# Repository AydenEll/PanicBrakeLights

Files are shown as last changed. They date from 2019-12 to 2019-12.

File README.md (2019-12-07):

# PanicBrakeLights [Version 1.0]
This repository shows how to add an automatically activated supplementary brake light system to a motorcycle.  The system will activate and strobe to attract attention when greater than average braking force is sensed.

Repository Contents
=========================
* **/img** - Image files for the README file
* **/hardware** - Circuit design information
* **/src** - Project code (*.ino file for Arduino)
* **/LICENSE** - The user license file (open)
* **/README.md** - Project guide (this document)

Requirements and Materials
=========================

**Libraries required:**
* **Adafruit ADXL343 by Adafruit** - [Adafruit ADXL343 Accelerometer Driver](https://github.com/adafruit/Adafruit_ADXL343)
* **Adafruit Unified Sensor by Adafruit** - [Adafruit Unified Sensor Driver](https://github.com/adafruit/Adafruit_Sensor)
* **Adafruit NeoPixel by Adafruit** - [Adafruit NeoPixel Library](https://github.com/adafruit/Adafruit_NeoPixel)

**Materials required:**
* Arduino-based microcontroller: [Adafruit Metro Mini](https://www.adafruit.com/product/2590) is used in my implementation (Adafruit Product ID 2590)
* [Adafruit ADXL343 Triple-Axis Accelerometer](https://www.adafruit.com/product/4097) (Adafruit Product ID 4097)
* Weather-resistant adhesive-backed LED strips: strips of WS2812B individually addressable LED modules such as [Adafruit NeoPixels](https://www.adafruit.com/product/1138) will be used--they are individually addressable and can be cut to any length (as small as one LED element)
* LM2596 DC-to-DC buck converter to step 12V down to 5V (to power system off motorcycle battery)
* Small breadboard to act as substrate and to maintain proper alignment of accelerometer
* Assorted bulk wire, jumper wires, and shrink tube
* Soldering station and soldering supplies including solder, flux, desoldering tools/wick, and a "third hand"

Build Instructions
=========================
The main circuit assembly is quite straightforward.  Using a small breadboard as a substrate, connect your Metro Mini, ADXL343, and LED strips (left and right) with the step-down power converter according to the following breadboard diagram and wiring schematic:
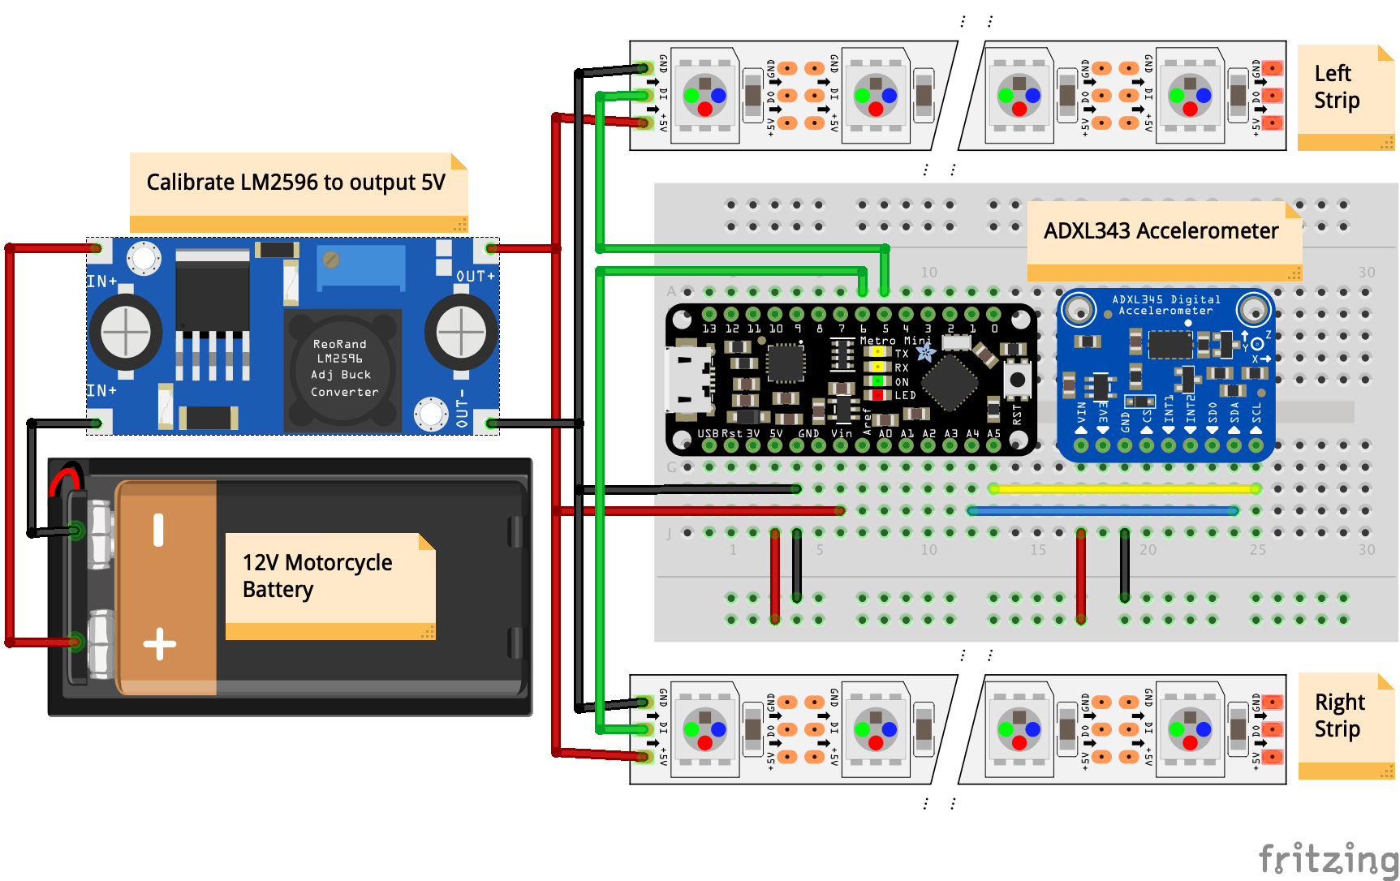
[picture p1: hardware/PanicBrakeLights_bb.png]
Breadboard Diagram

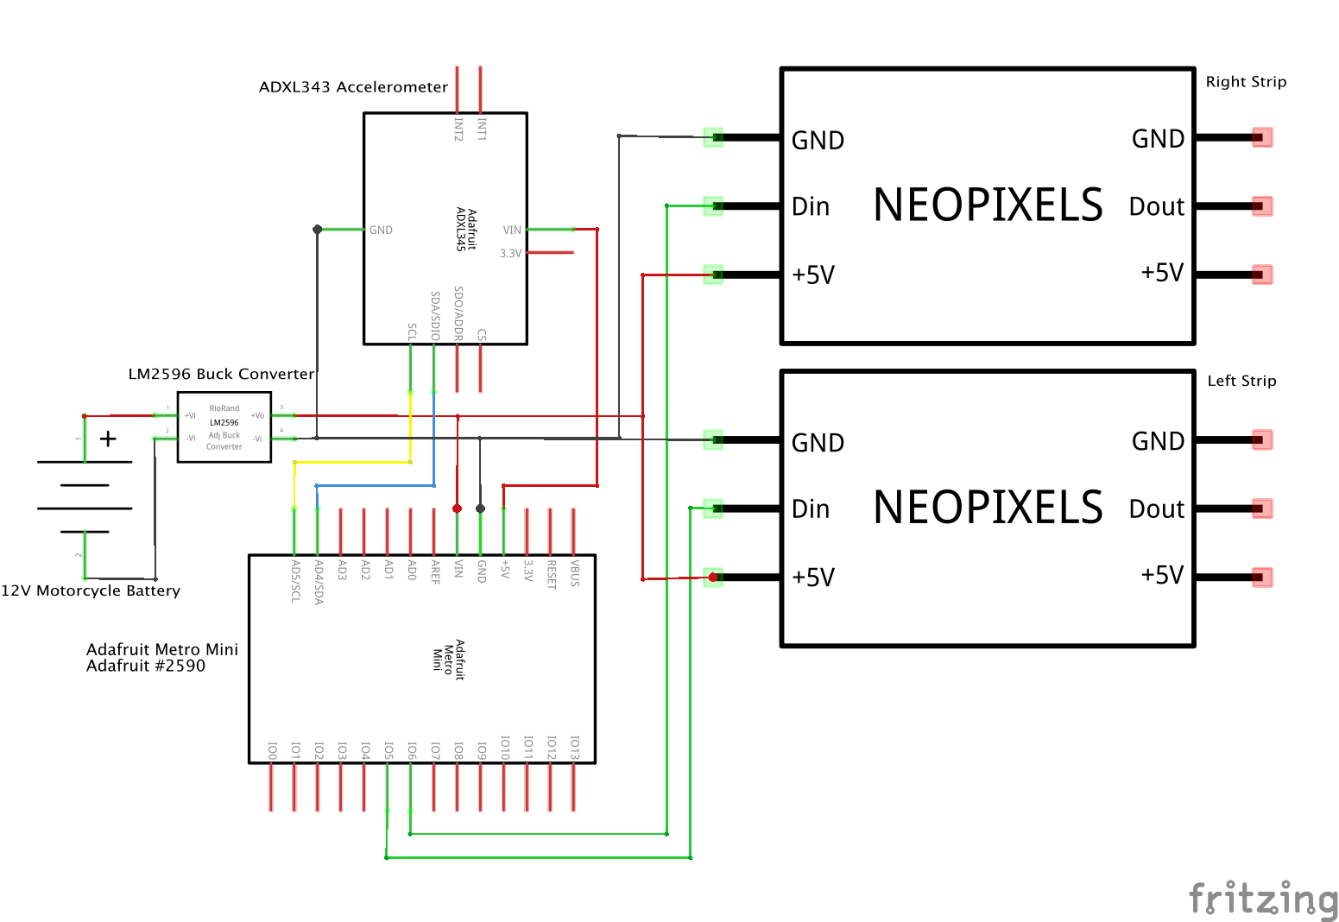
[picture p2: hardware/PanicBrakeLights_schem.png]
Wiring Schematic


You may be required to assemble the accelerometer and microcontroller by attaching the headers.  If so, insert the headers into a breadboard and set the device on the pins.  Then, solder each pin by heating the pin and solder pad on the board at the same time, then touching the solder to the pin and tip of the iron.  The result should look shiny and slightly concave and cover the hole entirely.  If the solder sticks out or forms ball-like structures, it has not properly bonded to the solder pad on the circuit board.  This is called a cold solder joint and it means that the joint is much weaker and will not conduct as well.  Re-heat the solder and hold the tip of the iron firmly to the pad on the board.  After a few seconds, the solder should flow properly and bond with the pad, resulting in a good connection.

<p float="center">
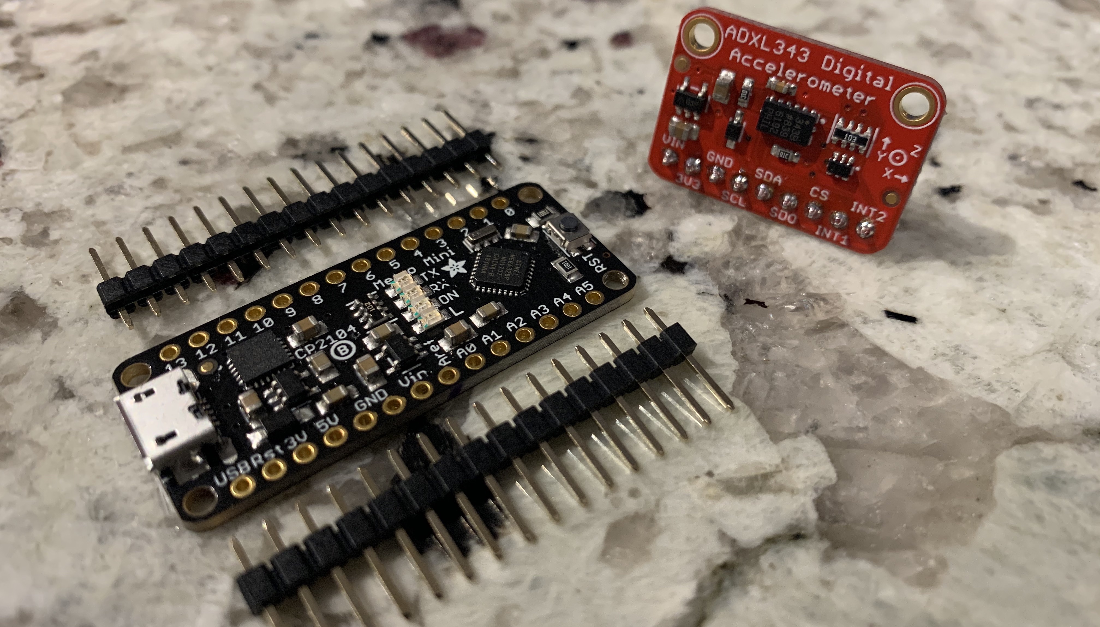
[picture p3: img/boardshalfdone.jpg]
One board finished, one to go
  
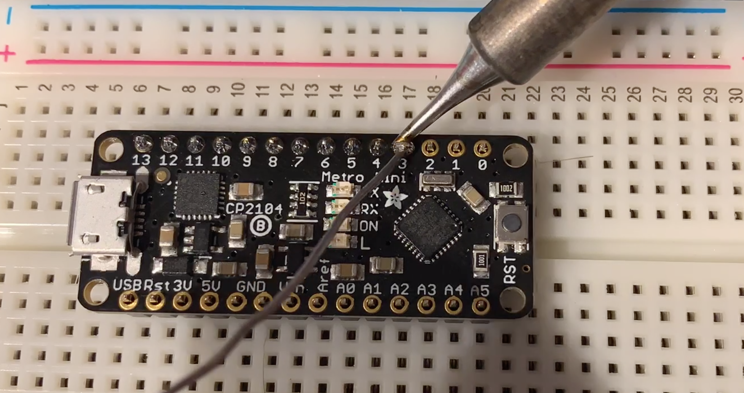
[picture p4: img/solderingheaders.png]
Solding Metro Mini headers
   
</p>

I was fortunate that my motorcycle had a large "blank canvas" in the form of the panniers, so I was able to play with the design of the LED strips and form them into arrows pointing to either side of the motorcycle.  I am aware that many motorcycles will not allow such luxuries, so you will need to adapt the strip design to your needs.  It is possible to cut the strips to any number of pixels in length, but it is important to ensure that any joints are weatherproofed with shrink tubing.  Finally, solder wire leads to the input and output pins of the step-down power converter.  It is best to be able to physically disconnect the power supply from all other devices, so use some kind of in-line connector.  This will serve to isolate all devices from power during calibration and allows easier retrofits or modifications to the system.

Following, you can see the process of preparing a strip for connections, tinning the contacts, attaching wire leads, and weatherproofing with shrink tube.

<p float="center">
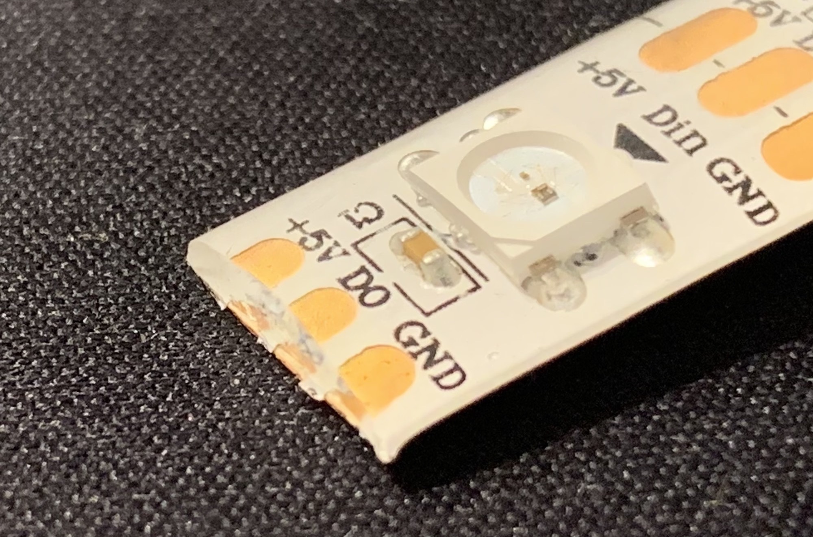
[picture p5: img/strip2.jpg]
Unprepared strip end
  
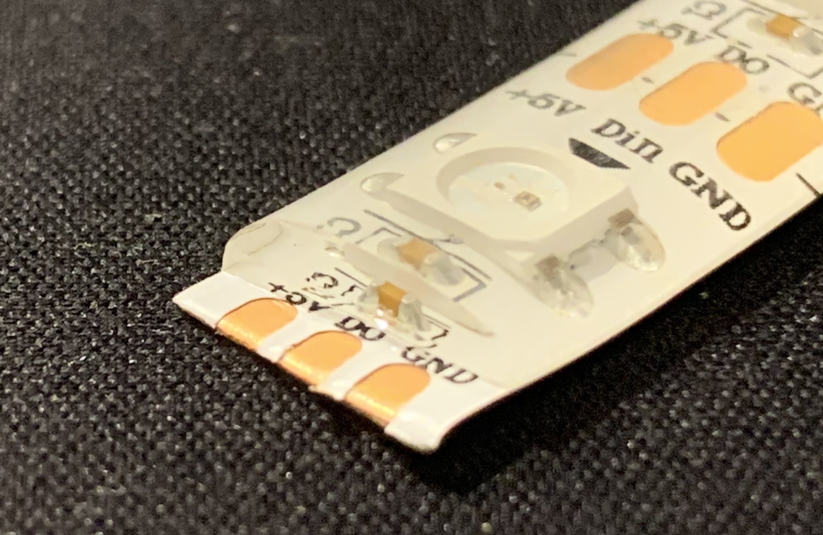
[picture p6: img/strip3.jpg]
Prepared strip end
   
</p>
<p float="center">
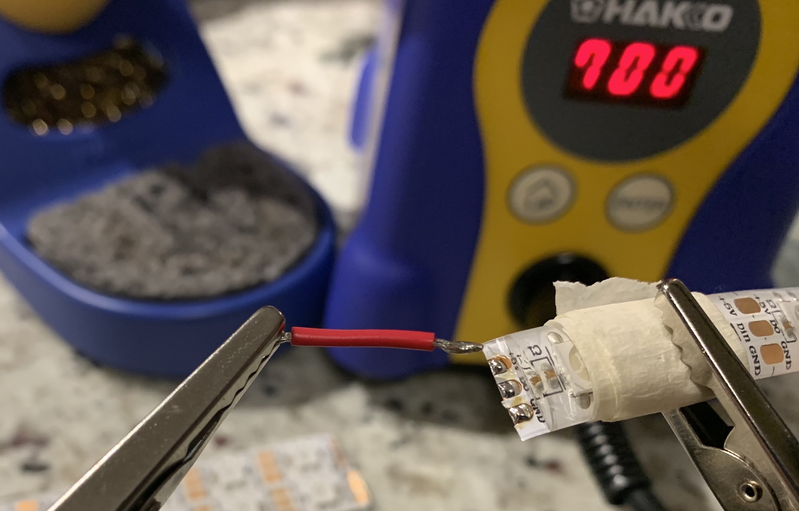
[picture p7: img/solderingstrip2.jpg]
Tinned strip contacts
  
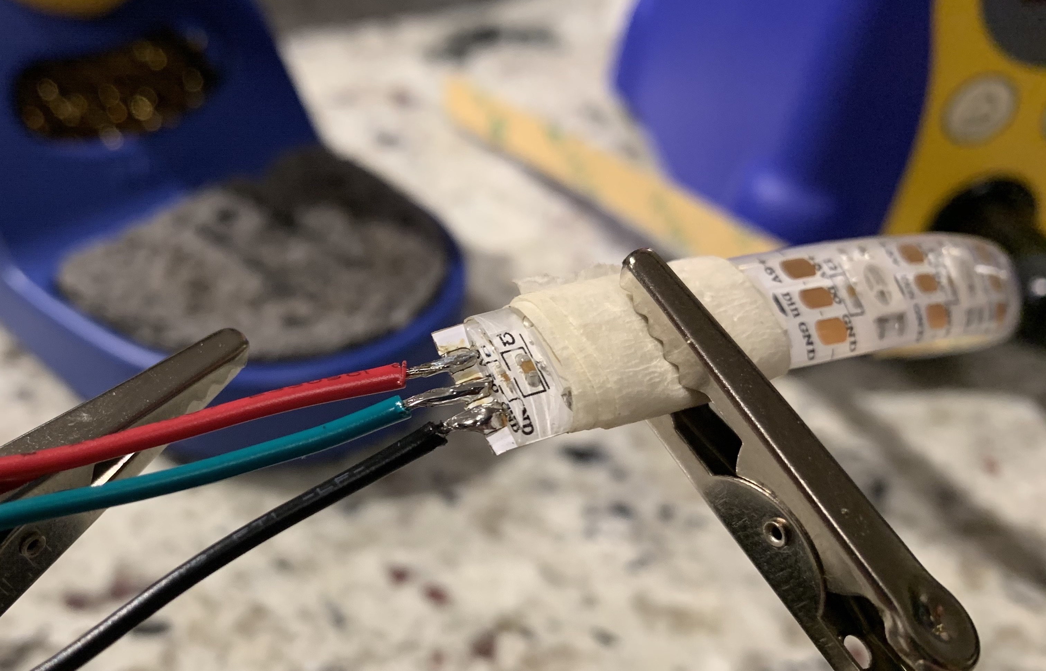
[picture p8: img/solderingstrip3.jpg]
Wires attached to strip end
   
</p>

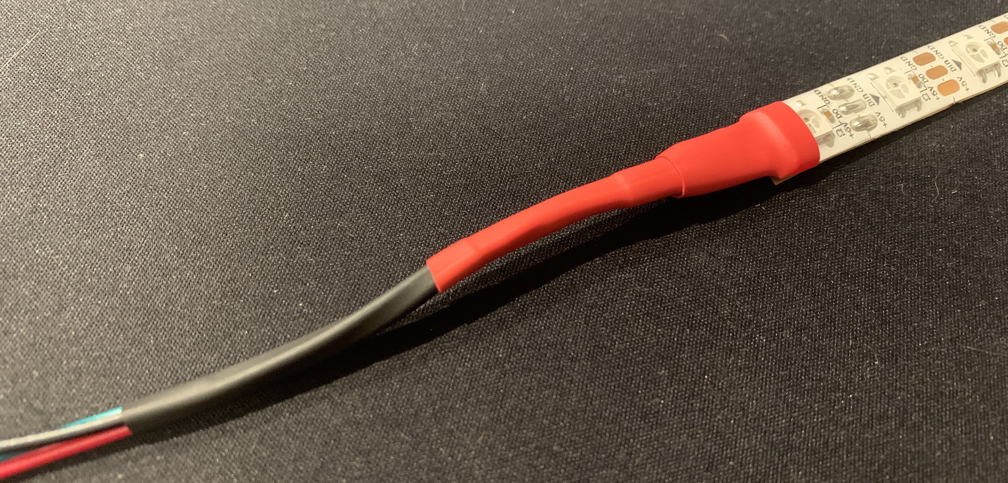
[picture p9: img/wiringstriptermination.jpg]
Weatherproofing connections with shrink tube


I created a custom wiring harness in order to facilitate a cleaner final install.  According to the wiring schematics above, create a wiring harness similar to the following where power is supplied to each +5v pin on the strips and the Vin pin on the Arduino and there is a shared ground between all devices.  I integrated the LED strip data lines into the power supply lines for each strip for a more streamlined package.  Again, ensure all connections are weatherproofed adequately.

Note: the accelerometer should be positioned on the motorcycle such that the X-axis arrow is pointing forward (along the longitudinal axis of the bike).

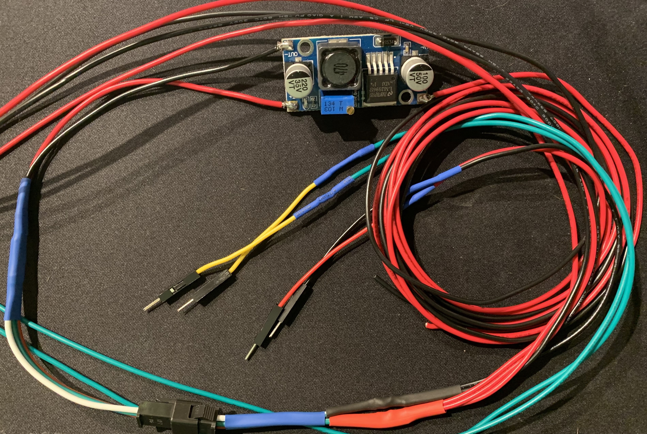
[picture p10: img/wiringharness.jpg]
Custom wiring harness


Once the system is installed on the motorcycle, the last stage is to run power lines from the positive and negative battery terminals to the inputs on the LM2596 power converter.  **Do not plug the power converter output into anything yet!  Calibrate it to output 5V by reading the output pins with a multimeter and turning the screw on the blue potentiometer before plugging in any devices!**

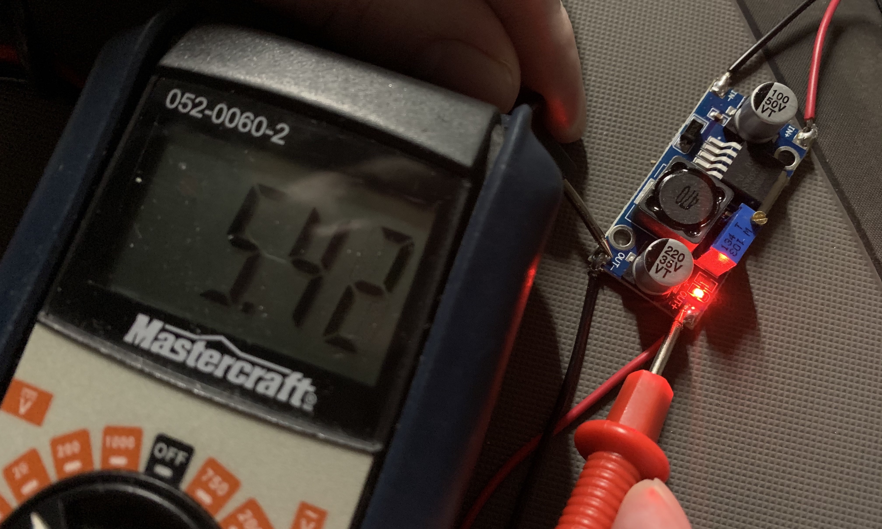
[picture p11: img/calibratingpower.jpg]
Calibrating step-down power converter


Usage
=========================
Once the hardware is assembled, perform the following preparatory operations to get it up and running:

* Install the Arduino IDE to program the Arduino-based microcontroller
* Install the requisite libraries mentioned above under **Requirements and Materials**
* Install the code listed in /src to the Arduino-based microcontroller
* Set LEDL_COUNT and LEDR_COUNT to the number of left and right LEDs, respectively

Once the above preparatory operations are complete and the step-down power converter output has been calibrated to 5V, double-check all wiring and then supply power to the strips and Arduino.  The device can be tested by shaking it (will impart enough negative acceleration to trigger strobing functionality).

If the initial test is successful, you may alter the threshold of the accelerometer to better suit your needs (supplied threshold is a medium value).  Use the provided thresholding helper functions to save accelerometer data to the built-in EEPROM and then retrieve it via the serial console.  See the following for the general process:

* Enable the StoreAcceleration helper function to record deceleration data to the EEPROM for thresholding.  It is advisable to set the loop delay to something like 250ms so the EEPROM isn't flooded with too many data points and so you can do multiple calibration runs before it runs out of storage.
* Perform several test runs on the motorcycle with varying degrees of braking force.
* Return the Arduino unit to your computer, disable the StoreAcceleration function and enable the PrintEEPROM function to review the accelerometer readings on the serial console.  Note: this resets the EEPROM memory location pointer back to the beginning so you can perform additional calibration runs if necessary.
* Determine which level of negative acceleration is best for your needs and set THRESHOLD to that value.

Below is the final install on the motorcycle and the system in action.
<p float="center">
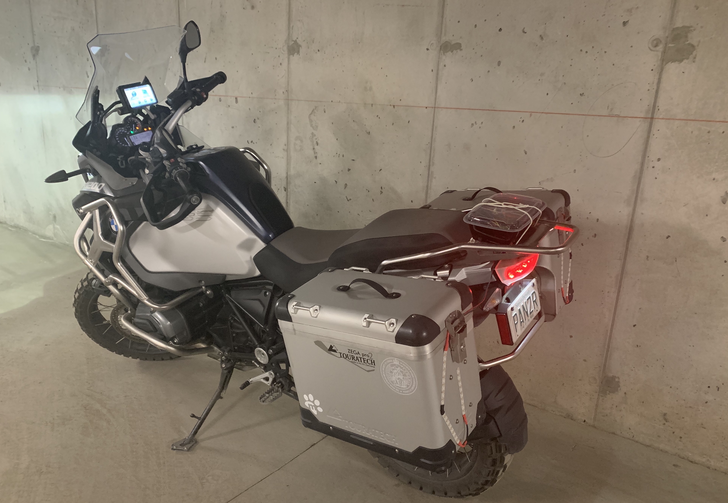
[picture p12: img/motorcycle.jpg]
Final Install
  
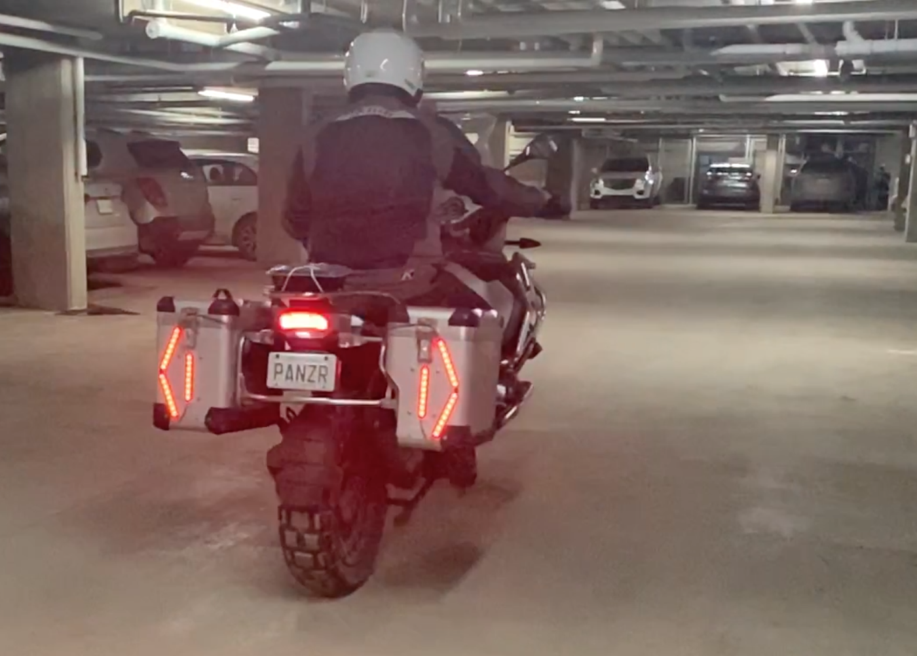
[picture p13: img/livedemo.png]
Live Demo
   
</p>

Finally, the obligatory glamour shot!
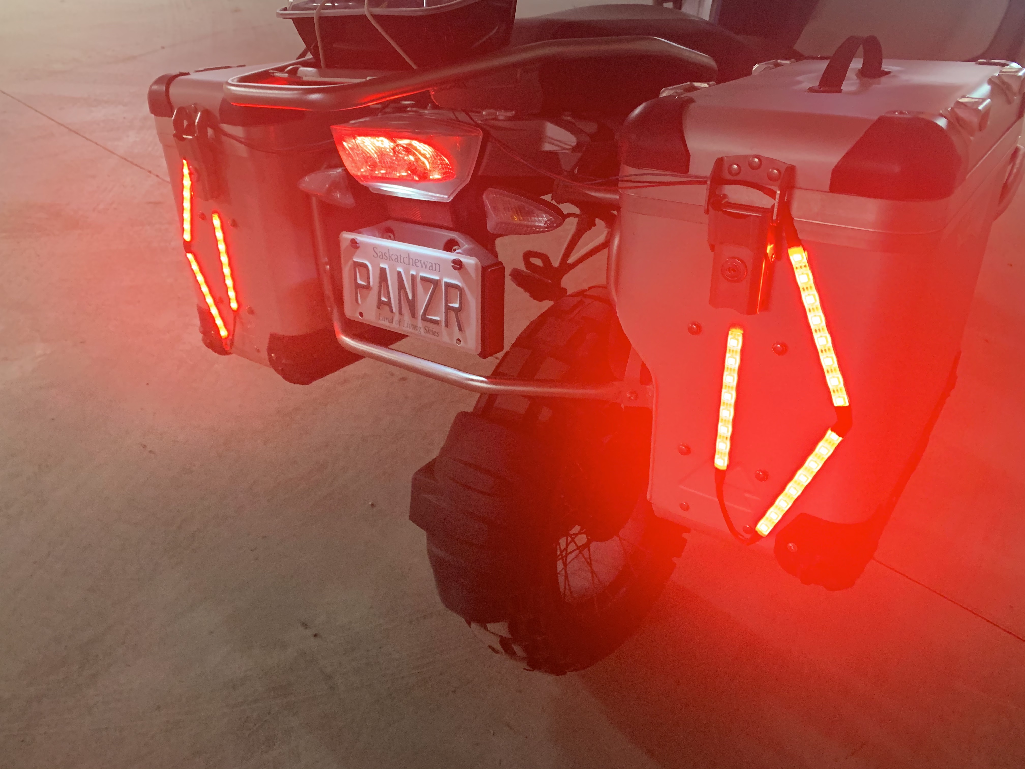
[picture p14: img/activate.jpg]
Beautiful, isn't it?


Credits
=========================
The inspiration for the project came from Instructables.com user *kristeller62* and their [Passive Brake Lights](https://www.instructables.com/id/passive-brake-light/) project.

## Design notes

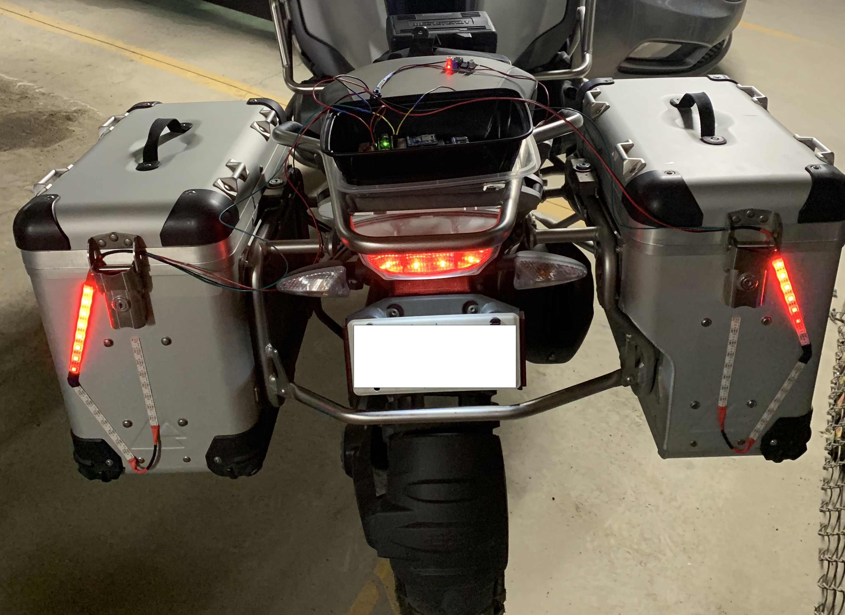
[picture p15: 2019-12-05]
img/demostationary.jpg

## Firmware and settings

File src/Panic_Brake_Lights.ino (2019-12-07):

/*
 * Panic Brake Lights
 * 
 * Purpose: To automatically activate strobing lights, affixed to the rear of a
 *          motorcycle, under situations of greater than normal braking force.
 *    
 * Required Hardware: 
 *        - Adafruit Metro Mini controller board is used
 *        - Adafruit ADXL343 Analog Devices accelerometer breakout board
 *        - LM2596 DC to DC buck converter to step down 12V supply from motorcycle
 *            to 5V for Metro Mini and LED strips
 *        - Strips of WS2812B LED modules to make up left and right side lights
 *            - each elements can be individually addressed
 *            - e.g. Adafruit NeoPixel strips
 * Setup:
 *        - Metro Mini Pin 5 to 560ohm resistor then to left LED strip data pin
 *        - Metro Mini Pin 6 to 560ohm resistor then to right LED strip data pin
 *        - Metro Mini Pin A5 (SCL) to ADXL343 clock pin
 *        - Metro Mini Pin A4 (SDA) to ADXL343 data pin
 *        - Metro Mini +5V out to Vin on ADXL343
 *        - Metro Mini GND to GND on ADXL343
 *        - +5V supply to Metro Mini Vin and +5V on left and right LED strip
 *        - GND from power supply shared to GND on Metro Mini and each LED strip
 * 
 * Created  November  8, 2019 (basic NeoPixel functionality tested)
 * Modified November 17, 2019 (NeoPixel refinements)
 * Modified November 23, 2019 (incorporated accelerometer code)
 * Modified November 30, 2019 (first setup on actual hardware and more refinements)
 * Modified December  4, 2019 (updated Strobe function constants; removed Wipe function)
 * Modified December  5, 2019 (helper functions for thresholding; removed BrightnessTest function)
 * Modified December  6, 2019 (accelerometer threshold set; program complete)
 * 
 * By Ayden Ell
 * 
 */

// Import libraries for LEDs, sensor, and serial communication
#include <Adafruit_NeoPixel.h>  // to control LED strips
#include <Wire.h>               // to use serial communication
#include <Adafruit_Sensor.h>    // for generic Adafruit sensor functionality
#include <Adafruit_ADXL343.h>   // for Adafruit ADXL343 accelerometer functionality
#include <EEPROM.h>             // for storing accelerometer data for thresholding

// Constants to reference LED strips
const int LEDL_PIN = 5;   // Left LED strip pin
const int LEDR_PIN = 6;   // Right LED strip pin
const int LEDL_COUNT = 24; // Left LED count
const int LEDR_COUNT = 24; // Right LED count

// Other constants
//*** Proper threshold still needs to be determined for accelerometer X axis ***//
const double THRESHOLD = -5.0; // Accelerometer threshold to trigger strobing effect
const uint32_t RED = 0xFF0000; // HEX colour red to be used by NeoPixel elements
const int BRIGHTNESS = 127;   // LED strip brightness (range 0 - 255)
const int DELAY = 10;         // default loop delay
const int CYCLES = 20;        // number of strobe cycles on triggered event (500ms each)
const int SHORT_BLINK = 50;   // duration for the LED strip OFF cycle
const int LONG_BLINK = 202;   // duration for the LED strip ON cycle
const int ELEMENT_DELAY = 2;  // default delay between LED strip elements activating
// Note: LONG_BLINK + (24 * ELEMENT_DELAY) should total 250ms
//       e.g. if ELEMENT_DELAY == 1, then LONG_BLINK = 226
//            else if ELEMENT_DELAY == 2, then LONG_BLINK = 202

// Global variable to store EEPROM memory location "pointer"
//  to aid in thresholding (used by helper functions)
int memoryLocation = 2;

// Declare NeoPixel objects
Adafruit_NeoPixel stripL(LEDL_COUNT, LEDL_PIN); // outer left strip
Adafruit_NeoPixel stripR(LEDR_COUNT, LEDR_PIN); // outer right strip

// Declare sensor objects
Adafruit_ADXL343 accel = Adafruit_ADXL343(12345);
sensors_event_t event;

void setup()
{
  Serial.begin(9600);
  accel.begin();

  // Set accelerometer range to +- 2G
  accel.setRange(ADXL343_RANGE_2_G);
  
  // Left outer strip setup
  stripL.begin();                   // Initialize NeoPixel strip object
  stripL.show();                    // Initialize to "off" (showing black)
  stripL.setBrightness(BRIGHTNESS); // Set strip brightness (max 255)

  // Right outer strip setup
  stripR.begin();                   // Initialize NeoPixel strip object
  stripR.show();                    // Initialize to "off" (showing black)
  stripR.setBrightness(BRIGHTNESS); // Set strip brightness (max 255)

  // Read memory location (stored at 0) from EEPROM and save in MEMORY_LOCATION
  EEPROM.get(0, memoryLocation);
}

void loop() 
{
  // Get new accelerometer sensor event and acceleration for each axis
  accel.getEvent(&event);
  double X = event.acceleration.x;
  // Unnecessary accelerometer data for X-axis pointing forward implementation
  //  but can be used for other implementations or program/build expansion
  // double Y = event.acceleration.y;
  // double Z = event.acceleration.z;

  // Three useful helper functions to debug and threshold the accelerometer
  //  can be enabled and disabled as necessary (turn all off in final build)
  //PrintAcceleration(X, Y, Z);
  //StoreAcceleration(X);
  //PrintEEPROM();

  // If negative X acceleration is less than the threshold (breaking hard),
  //  activate strobing lights (each strobe cycle takes 500ms)
  if(X <= THRESHOLD)
    for (int i = 0; i < CYCLES; i++)
      Strobe(stripL, stripR, RED);

  delay(DELAY); //temporarily increase to ~250ms for thresholding
}

/*  PrintAcceleration
 *  Purpose: Print accelerometer data to serial console 
 *    for thresholding and debugging
 *  Parameters:
 *    <1> x - the X-axis acceleration
 *    <2> x - the Y-axis acceleration
 *    <3> x - the Z-axis acceleration
 *  Returns: void
 */
void PrintAcceleration(double x, double y, double z)
{
  Serial.print("X: "); Serial.print(x);
  Serial.print("  Y: "); Serial.print(y);
  Serial.print("  Z: "); Serial.print(z);
  Serial.println("  (m/s^2)");
}

/*  StoreAcceleration
 *  Purpose: Store acceleration data into EEPROM if it is of interest 
 *    but only stores acceleration values less than -1.0 and if EEPROM not full
 *  Parameters:
 *    <1> X - value to be stored
 *  Returns: void
 */
void StoreAcceleration(double value)
{
  // If negative acceleration is less than -1.0, store value in memory,
  //   increment memory location pointer, and store new pointer at address 0
  if((value < -1.0) && (memoryLocation < 1000)) // 1024 bytes of EEPROM
  {
    EEPROM.put(memoryLocation, value); // store "value" at memoryLocation
    memoryLocation += 8; // increment location by 8 bytes (for double)
    EEPROM.put(0, memoryLocation); // store new memory location at 0
  }
}

/*  PrintEEPROM
 *  Purpose: Prints contents of EEPROM and resets memory pointer back to beginning (2)
 *  Parameters: n/a
 *  Returns: void
 */
void PrintEEPROM()
{
  // Print accelerometer data to the serial console
  for(int i = 2; i <= memoryLocation - 8; i += 8)
  {
    float temp;
    EEPROM.get(i, temp);
    Serial.print("X: ");
    Serial.print(temp);
    Serial.print("m/s^2 at location ");
    Serial.println(i);
  }
  // Reset memory location back to the start of the EEPROM
  memoryLocation = 2;
  EEPROM.put(0, memoryLocation);
}

/*  Strobe
 *  Purpose: To strobe both left and right LED strips; total time per cycle is 500ms.
 *  Parameters:
 *    <1> strip1 - the first strip object to fill, passed by reference
 *    <2> strip2 - the second strip object to fill, passed by reference
 *  Returns: void
 */
void Strobe(Adafruit_NeoPixel & strip1, Adafruit_NeoPixel & strip2, uint32_t colour)
{  
  // Fill both strips with given colour with small delay (looks animated)
  for(int i = 0; i < strip1.numPixels(); i++)
  {
    strip1.setPixelColor(i, colour);
    strip1.show();
    strip2.setPixelColor(i, colour);
    strip2.show();
    delay(ELEMENT_DELAY);
  }
  delay(LONG_BLINK);
  
  // Clear both strips for short duration
  strip1.clear();
  strip1.show();
  strip2.clear();
  strip2.show();
  delay(SHORT_BLINK);

  // Quickly flash the lights twice (kind of a "chirping" effect)
  for (int i = 0; i < 2; i++)
  {
    // Fill both strips with given colour without delay between elements
    for(int j = 0; i < strip1.numPixels(); i++)
    {
      strip1.setPixelColor(i, colour);
      strip1.show();
      strip2.setPixelColor(i, colour);
      strip2.show();
    }
    delay(SHORT_BLINK);

    // Clear both strips for short duration
    strip1.clear();
    strip1.show();
    strip2.clear();
    strip2.show();
    delay(SHORT_BLINK);
  }
}

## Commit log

2019-12-02 Revised Software
    Revised software tested and working with final hardware install on motorcycle. Accelerometer still needs to be thresholded.
2019-12-04 Updated Code
    Updates to main code including changes to the strobe function (added "chirp" and intended total time), updated constants, removed unnecessary comments, and removed unnecessary Wipe function. Note: se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
2019-12-05 Revised Software (with helper functions)
    Added multiple helper functions to aid with thresholding accelerometer using EEPROM and removed the last of the unnecessary test code (brightness test).
2019-12-05 Hardware Schematic Directory
    Includes Fritzing file and diagrams.
    [PanicBrakeLights.fzz]
2019-12-06 Updated README
    Updated README document to include build, install, and calibration directions.
2019-12-06 Updated Schematics
    Updated schematics to fix a minor error in the notes for a device.
    [PanicBrakeLights.fzz]
